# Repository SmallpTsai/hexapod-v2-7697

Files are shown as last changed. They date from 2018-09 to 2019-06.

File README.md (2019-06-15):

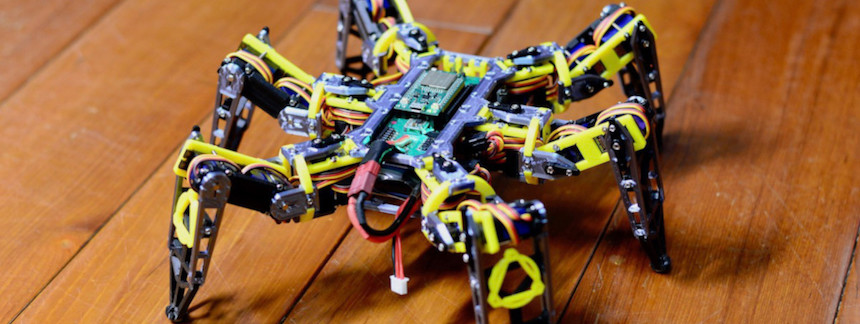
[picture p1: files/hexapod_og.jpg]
banner


# hexapod-v2-7697

> 中文版本請看 [這裡](README_tw.md)

Hexapod v2 using Linkit 7697

This is a Hexapod project.

You can use any mobile phone (iOS or Android) to control the movement of hexapod (move foreward, backward, etc...).

See demo video: https://youtu.be/NJ7DdDEcq3U & https://youtu.be/To2Y6Mhu-CE to get the idea.




> More videos can be found at https://smallptsai.github.io/hexapod-web/

## Brief introduction

* **Remote control** is done via `BLE` of `Linkit 7697`
* It has 6 legs, each leg has 3 joint. So there are total `18` **Servo motors** (TowerPro `MG92B`)
* Linkt 7697 dont have so many **PWM control**, so NXP `PCA9685` x 2 are used to control these servo motors
* **Power** comes from a `2S Lipo battery (7.4v)`. Also 7 x `mini360 DC-DC` step down voltage regulator are used. One to provide `5V` to Linkit 7697, The other six to provide `6V` to each legs (1 mini360 serve 3 servo)
* The **body** is 3D printed PLA. I use `Prusa i3 MK2S`, a really good 3D printer.
* Everything (3D STL, PCB schematic, 7697 source code) are included in the project under **GPL license**, Happy making!

## Skill requirement

If you want to make one hexapod by yourself. You should at least knows how to:

* Mechanism part
    * Use `3D printer` to print a model.
    * Able to adjust 3D model to fit your custom need.
* Electronics
    * Make a `PCB` (suggest to use professional PCB services)
    * Soldering `SMD` component (0805 and TSSOP28)
    * How to use/charge/store `LIPO batteries`
* Software
    * Use `Linkit 7697` (ie. upload and run any program)
    * Use `LRemote` to communicate 7697 and your mobile phone

## Table of Content

1. [Mechanism](mechanism/) - How to build the body
1. [Electronics](electronics/) - Circuit explanition
1. [Software](software/) - The software running on Linkit 7697

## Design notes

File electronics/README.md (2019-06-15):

# Electronics

## Connection Diagram

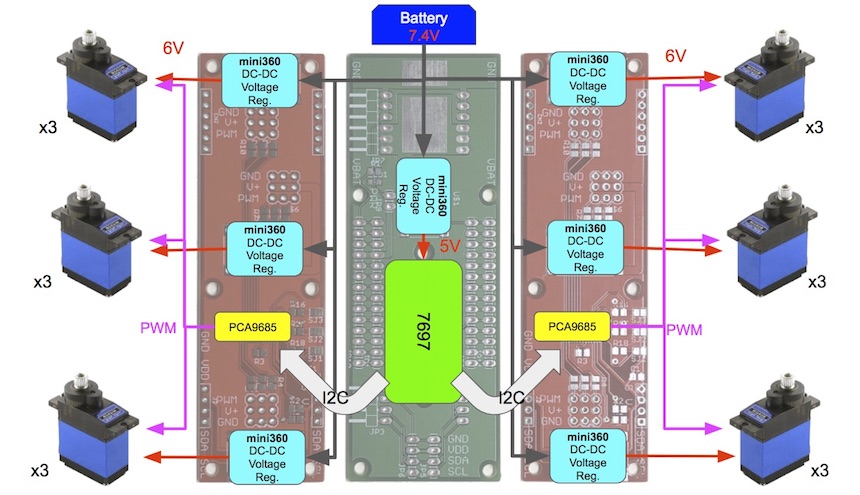
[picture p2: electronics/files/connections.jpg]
connections


## Bill of Materials (BOM)

### PCB

Name | Thumbnail | Required | Note |
-------- | --------- | -------- | ---- | 
main | main | 1 |
sub | sub | 2 | there is a difference (SJ1) between<br>the 2 PCB, refer to below

### Components

Name | Thumbnail | Required | Note |
-------- | --------- | -------- | ---- | 
[Linkit 7697](https://labs.mediatek.com/zh-tw/platform/linkit-7697) |  | 1 |
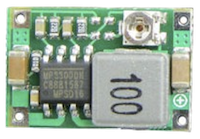
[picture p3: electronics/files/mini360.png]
[mini360 DC-DC](https://www.aliexpress.com/w/wholesale-mini360-dc-dc.html) Buck voltage regulator |  | 7 | adjust to 5V
[PCA9685](https://cdn-shop.adafruit.com/datasheets/PCA9685.pdf) (TSSOP28)|  | 2 | TSSOP28 |
Resistor: 220 ohm (0805) | | 18 | SMD |
Resistor: 10K ohm (0805) | | 12 | SMD |
Resistor: 470 ohm (0805) | | 1 | SMD |
LED: green or any color (0805) | | 1 | SMD |
Capacitor: 10 uF (0805) | | 2 | SMD |
14 pin 2.54mm female header | | 4 |
4 pin 2.54mm female header | | 2 |
6 pin 2.54mm female header | | 2 |
4 pin 2.54mm 90 degress male header | | 2 |
6 pin 2.54mm 90 degress male header | | 2 |
4 pin 2.54mm male header | | 2 |
3 pin 2.54mm male header (black) | | 6 |
3 pin 2.54mm male header (yellow) | | 6 |
3 pin 2.54mm male header (red) | | 6 |
2 pin 2.54mm male header | | 1 |
Jumper 2.54mm | | 1 |

## PCB detail

##### Software 

Please use **Eagle 7.7** software to open schematic files (main.sch/main.brd and sub.sch/sub.brd)

Eagle 7.7 can be found at http://eagle.autodesk.com/eagle/software-versions/1

    Note.
    7.7 is an old and free version of Eagle. 
    Latest Eagle is not free anymore unless you are students

##### Manufacture

There are a lot of online service that can manufacture PCB/PCBA for you (just google `PCB/PCBA`).

Seeed (https://www.seeedstudio.io/fusion_pcb.html) is one of them.

They also provide instructions of generating necessary Gerber files at http://support.seeedstudio.com/knowledgebase/articles/1176532-how-to-generate-gerber-file.

### Main

`main.brd`/`main.sch`

##### Schematic

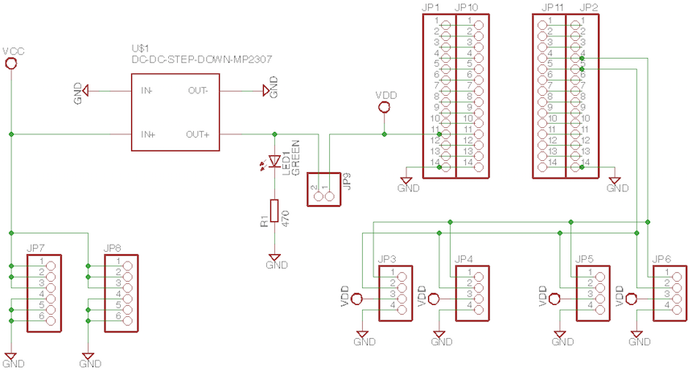
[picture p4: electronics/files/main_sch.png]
main_sch


    Note.
    `MP2307` refer to mini360 DC-DC converter

##### Layout

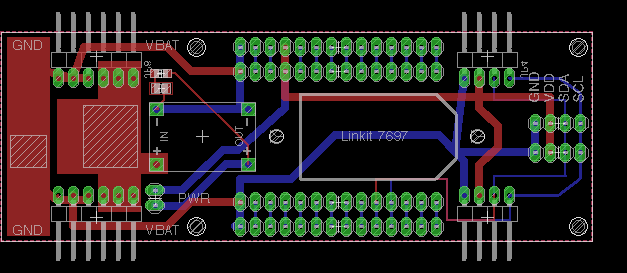
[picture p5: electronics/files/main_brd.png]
main_brd


##### PCB

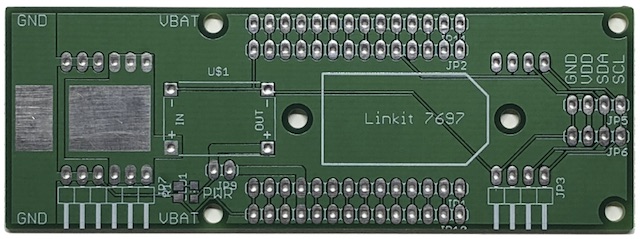
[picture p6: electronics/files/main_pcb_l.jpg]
main_pcb


### Sub (x2)

`sub.brd`/`usb.sch`

> There is 1 difference between left and right PCB. The SJ1 of right PCB is left open, but `SJ1` of left PCB should be **closed**. (This is i2c address setting of PCB9865)

##### Schematic

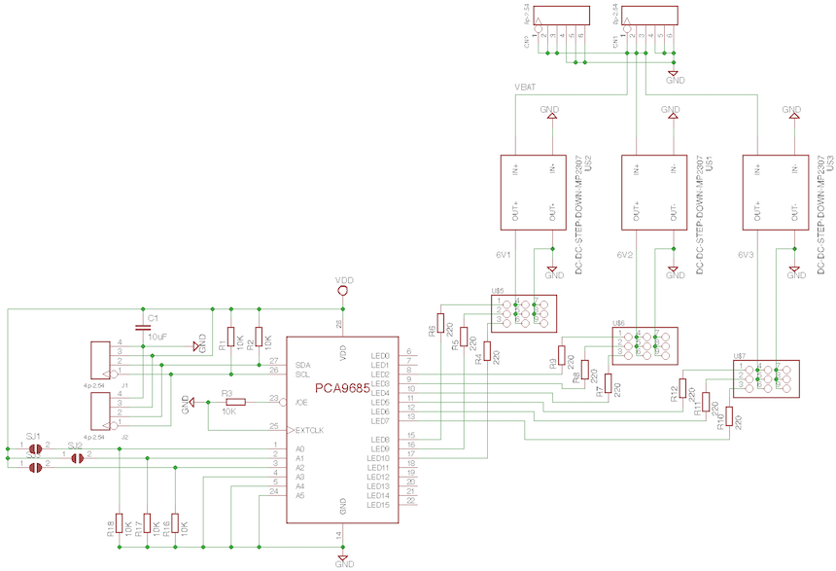
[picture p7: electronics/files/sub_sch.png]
sub_sch


    Note.
    `MP2307` refer to mini360 DC-DC converter

##### Layout

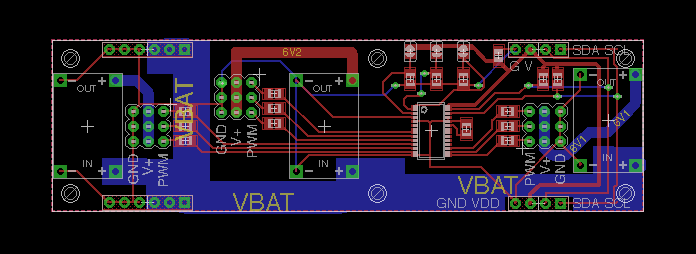
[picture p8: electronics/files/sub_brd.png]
sub_brd


##### PCB

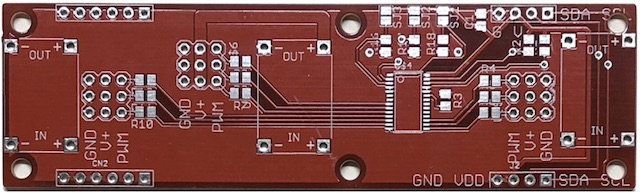
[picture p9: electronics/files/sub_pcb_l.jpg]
sub_pcb


## Servo Connection

Each leg of hexapod has 3 servos (body, thigh, foot), refer to below diagram for correct connection

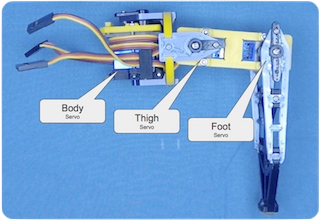
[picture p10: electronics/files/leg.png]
leg


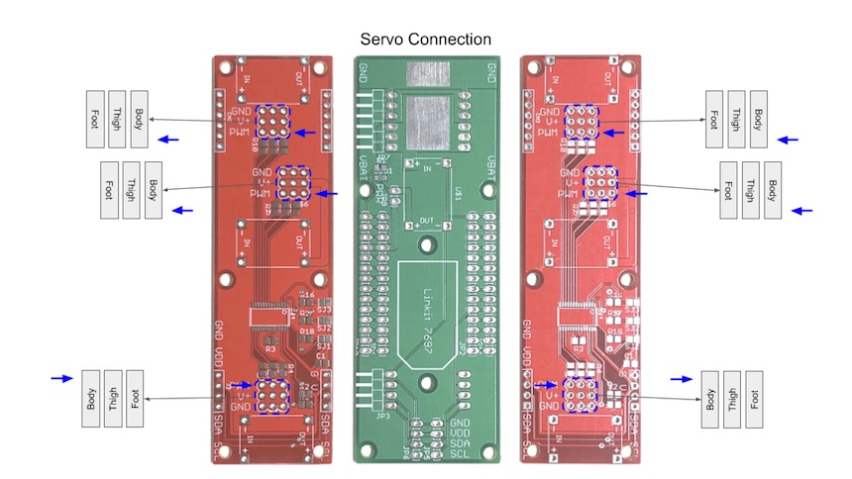
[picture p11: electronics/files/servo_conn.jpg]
servo_conn


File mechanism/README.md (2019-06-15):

# Mechanism

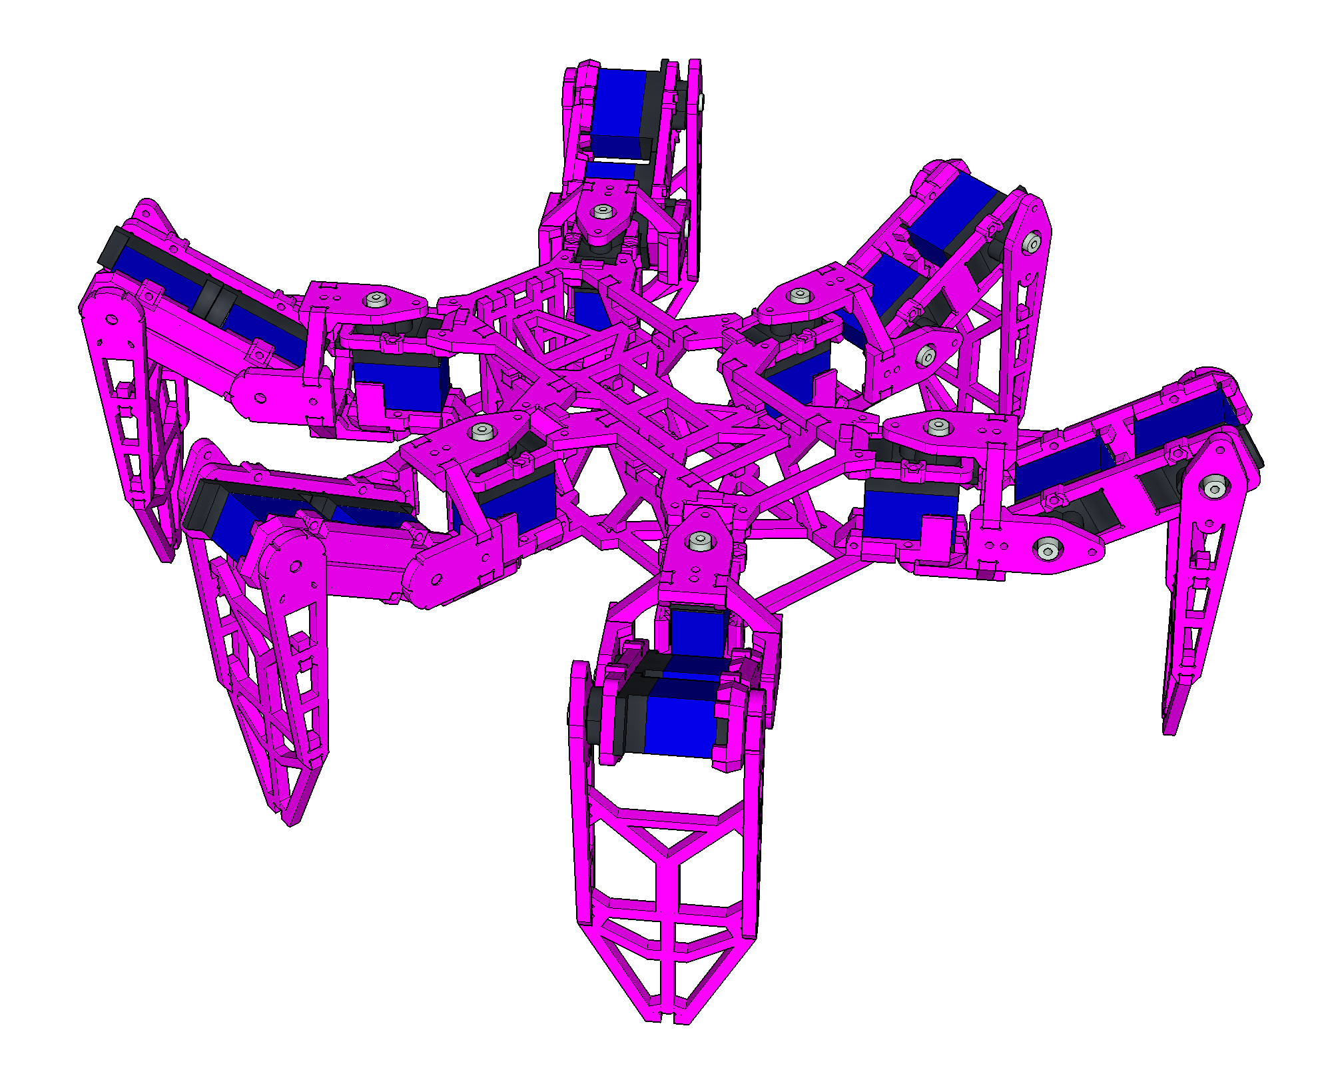
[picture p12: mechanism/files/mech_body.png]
Body


## Bill of Materials

[BOM](BOM.md)

## Leg Assemble

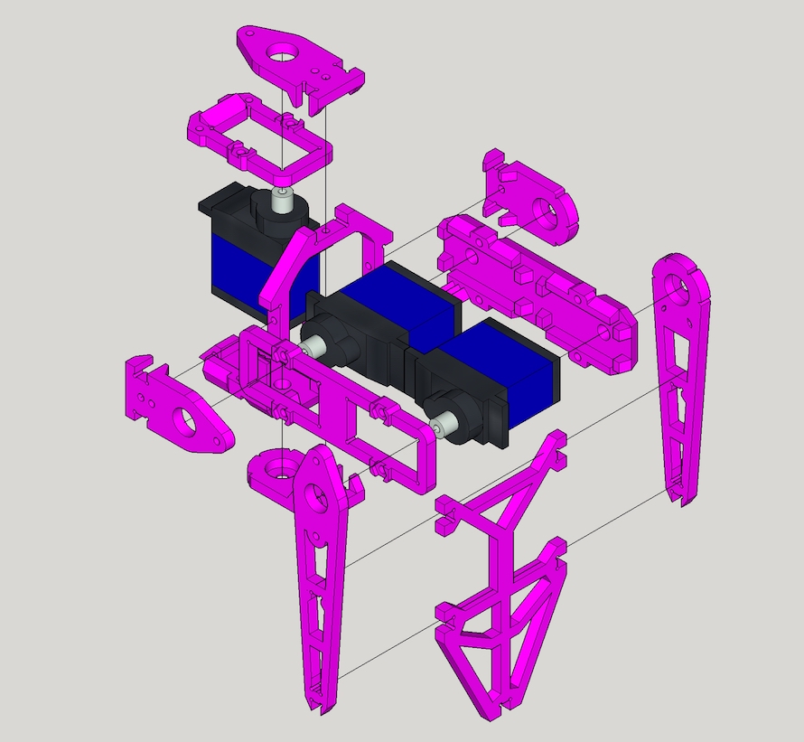
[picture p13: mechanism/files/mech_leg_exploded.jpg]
LegAssemble


Please check [Leg Assemble](LEG.md) for more detail instructions

Leg assembly instruction video https://youtu.be/oaAE5fC09KQ is also available.


> Note. Total 6 Legs are required.

## Body Assemble

TBD

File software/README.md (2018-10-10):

# Software

Software contain 2 parts, one is software of running on Linkt 7697 (an arduino C++ program), another is path generation (a python program).

* hexapod7697: an arduino program running on Linkit 7697
* pathTool: a python program that generate 3D points header, included by `hexapod7697`

## hexapod7697

Files/Folder | Description |
------------ | ----------- |
src/normal_mode | provide normal calibration (forward/backward/turn left/turn right/rotate/etc...) |
src/setting_mode | provide calirbration functions, to make sure servo is correctly aligned. |
src/linkit_control/ | UI control helper |
src/hexapod | hexapod class |
src/hexapod/hal | Hardware Abatraction Layer to running on Linkit 7697 |

> Note hexapod7697 use c++11 and STL, you may encounter problem if want to port it on pure Arduino platform.

#### Normal Mode UI

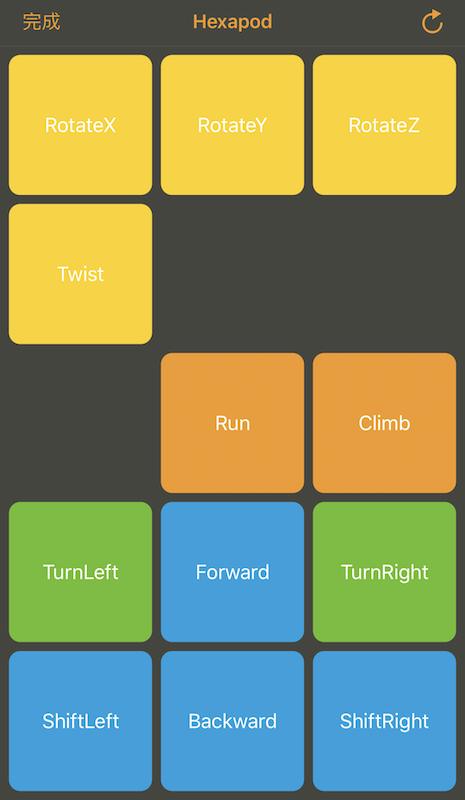
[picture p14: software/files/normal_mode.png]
normal


#### Setting (Calibration) Mode UI

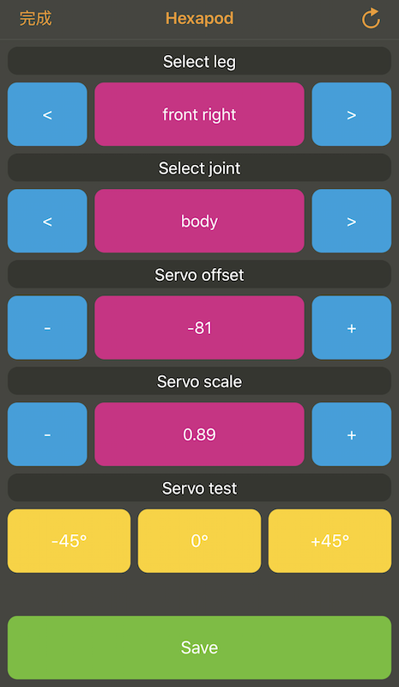
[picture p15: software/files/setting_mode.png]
setting


During Linkit 7697 boot up, quick press the user button. 

LRemote App will display above UI.

It is used to adjust the settings of each servo, make sure they align to center.

> Note. Dont press user button when power on, but just after power on.

## pathTool

* Python compatibility:
    * 3.x: ok.
    * 2.x: not verified. 
* Required package
    * numpy: `pip3 install numpy`

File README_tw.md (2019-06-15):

banner

# hexapod-v2-7697

Hexapod v2 using Linkit 7697

這是個 Hexapod (六足昆蟲) 專案

可以用任何手機 (iOS 或 Android) 來控制它的動作 (包括前進，後退，扭動等等...)

可參考以下的 Youtube 影片 https://youtu.be/NJ7DdDEcq3U & https://youtu.be/To2Y6Mhu-CE




> 在 https://smallptsai.github.io/hexapod-v2-7697/ 可以看到更多影片

## 簡介

* 利用 `Linkit 7697` 的 `BLE` 藍牙功能來作到 **遙控**
* 它有六隻腳，每隻腳各有三個關節，總共使用了 `18` 個 **伺服馬達** (TowerPro `MG92B`)
* Linkit 7696 沒有這麼多個 PWM 可用，所以使用了二顆 NXP 的 `PCA9685` 來控制這麼多個伺服馬達
* 動力使用 7.4v 的鋰電池 `2S Lipo battery (7.4v)`, 另外也用了 7 個 `mini360 DC-DC` 穩壓電路，其中 1 個供電給 Linkit 7697, 其它 6 個各負責一隻腳 (三個伺服馬達) 的電力
* 機身則使用 3D 列印 (PLA材質)
* 所有東西  (模型STL檔案, PCB電路圖, 7697代碼) 都以 GPL license 開源, Happy making!

## 技能需求

如果你也想要實現這個專案，會需要以下的技能:

* 機構部分
    * 會使用 `3D 列印`
    * 能夠微調 3D 模型以符合自己的需求 (例如, 使用不同的伺服馬達)
* 電路部分
    * 洗 `PCB` 電路板 (建議找專業 PCB 服務)
    * 焊接 `SMD` 元件 (0805 和 TSSOP28 封裝)
    * 知道如何使用鋰 (`Lipo`) 電池 (充電和保存)
* 軟體部分
    * 使用 `Linkit 7697` (ie. 編譯和上傳程式)
    * 使用 `LRemote` 來連接 7697 和手機

## Table of Content

1. [機構](mechanism/) - 如何組裝3D件 (English only)
1. [電路](electronics/) - 電路說明 (English only)
1. [軟體](software/) - 7697上的軟體 (English only)

## FAQ

1. 如何校正 / 為什麼腳的位置不正

    Calibration 在軟體內有內建, Reboot 後時按一下 7697 上的 USR key, 再用手機連會進到另一個 UI, 可以針對每個 Servo 去調中心點 (offset) 和 比例 (scale), 3d 件上都有個溝槽可以對 0度, 45度和 -45度, 對好後再按 Save 存檔

1. Servo 如何連接, 順序是什麼

    順序都是由內到外, body -> thigh -> foot，不過 layout 時會了走線好看, 有一隻腳的方向是反的，可以在 calibration 時切到不同位置按 45~0~-45度動看看來調整
    請參照 [electronics/#servo-connection](electronics/#servo-connection)

1. 在調整/校正時，左右 Servo 連動，正常嗎?

    不正常, 左右兩張板子有一個地方 (i2c address) 不同，左邊的PCB板的 SJ1 要焊起來
    請參照 [electronics/#sub-x2](electronics/#sub-x2)

1. 請問校正的標準姿勢為何? 例如人形立正或大字型

    所有的關節都在 0 度的位置, 是個 ㄇ 型
    校正要先回到 offset/scale 0 的情況, 再重鎖 servo 擺臂盡量到置中位置後，再用軟體微調~

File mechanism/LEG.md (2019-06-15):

# Leg Assemble Instruction

Leg assembly instruction video https://youtu.be/oaAE5fC09KQ is also available.


## Preparation

For one leg, you will need 3 MG92B servo and below printed parts

Filename | Thumbnail | Required |
-------- | --------- | -------- |
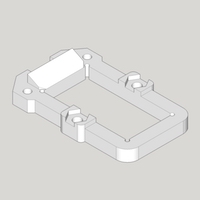
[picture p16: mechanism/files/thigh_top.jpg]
thigh_top
thigh_top |  | 1 |
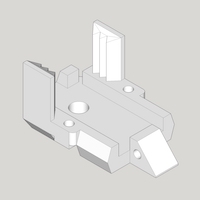
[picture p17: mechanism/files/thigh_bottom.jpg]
thigh_bottom
thigh_bottom |  | 1 |
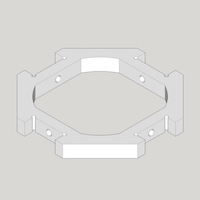
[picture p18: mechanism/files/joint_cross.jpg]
joint_cross
joint_cross |  | 1 |
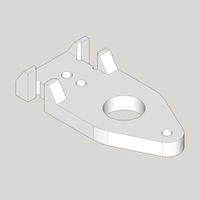
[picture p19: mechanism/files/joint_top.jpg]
joint_top
joint_top |  | 2 |
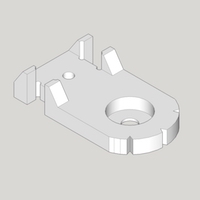
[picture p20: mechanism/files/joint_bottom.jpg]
joint_bottom
joint_bottom |  | 2 |
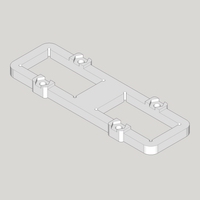
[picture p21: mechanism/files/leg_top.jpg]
leg_top
leg_top |  | 1 |
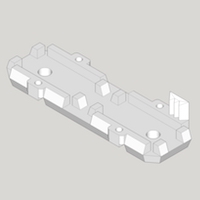
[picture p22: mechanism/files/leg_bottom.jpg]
leg_bottom
let_bottom |  | 1 |
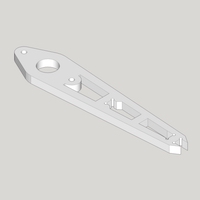
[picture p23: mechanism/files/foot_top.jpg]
foot_top
foot_top |  | 1 |
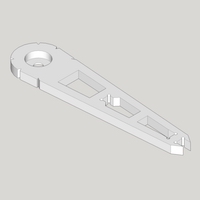
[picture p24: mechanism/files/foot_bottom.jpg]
foot_bottom
foot_bottom |  | 1 |
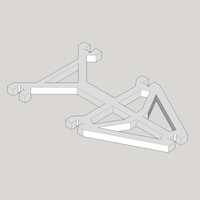
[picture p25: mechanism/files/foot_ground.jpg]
foot_ground
foot_ground |  | 1 |
foot_tip | foot_tip | 1 |

## Step 1

LegAssemble1

Combine `thigh_top`, `MG92B` and `thigh_bottom`, use M2x30mm screw and nut to secure them together.

## Step 2

LegAssemble2

Grab one `joint_cross`, `joint_top` and `joint_bottom` and combine them

## Step 3

LegAssemble3

First put 2 x `MG92B`, `leg_top` and `leg_bottom` together with M2x30mm screw and nut.
Then attach `joint_top` and `joint_bottom` altogether

## Step 4

LegAssemble4

Grab `foot_top`, `foot_bottom` and `foot_ground` (and `foot_top`) and assemble them.

## Finish!

LegAssemble5

Great, you got 1 leg done, 5 more to go :)

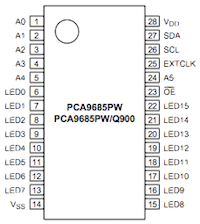
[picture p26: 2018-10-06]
electronics/files/pca9865.png

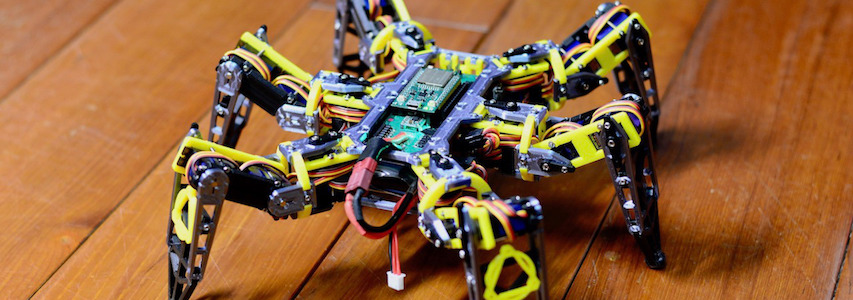
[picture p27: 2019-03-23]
docs/images/jumbotron-bg.jpg

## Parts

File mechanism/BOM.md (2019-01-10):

# Bill of Materials

## Servo - MG92B

Servo is the key component. I use TowerPro [MG92B](http://www.towerpro.com.tw/product/mg92b/). It has metal gear (important!).
An hexapod requires 18 of them.

>    The dimension of 3d printed part is highly depended on servo's dimension.<br>
>    Modification is required if you want to use other alternative servo. 

>    TowerPro MG92B can be found on Ebay seller [servohorns959](https://www.ebay.com/usr/servohorns959), which is listed on TowerPro official website ([Link] (http://www.towerpro.com.tw/about-us-2/)). <br>I also got mime servo from him.

## 3D-Printed Parts

### Body x 1

Filename | Thumbnail | Required |
-------- | --------- | -------- |
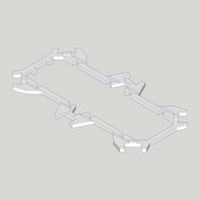
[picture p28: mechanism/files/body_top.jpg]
body_top
body_top |  | 1 |
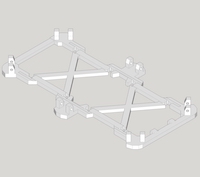
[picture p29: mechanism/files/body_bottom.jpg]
body_bottom
body_bottom |  | 1 |
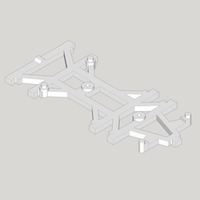
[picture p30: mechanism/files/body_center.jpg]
body_center
body_center |  | 1 |
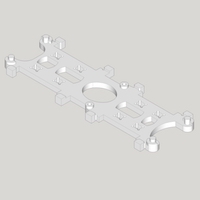
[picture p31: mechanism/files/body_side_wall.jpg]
body_side_wall
body_side_wall |  | 2 |
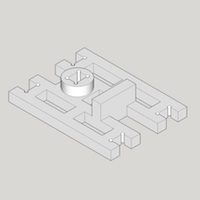
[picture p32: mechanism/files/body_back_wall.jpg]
body_back_wall
body_back_wall |  | 1 |

### Leg x 6

Filename | Thumbnail | Required |
-------- | --------- | -------- |
thigh_top | thigh_top | 1 (x6) |
thigh_bottom | thigh_bottom | 1 (x6) |
joint_cross | joint_cross | 1 (x6) |
joint_top | joint_top | 2 (x6) |
joint_bottom | joint_bottom | 2 (x6) |
leg_top | leg_top | 1 (x6) |
let_bottom | leg_bottom | 1 (x6) |
foot_top | foot_top | 1 (x6) |
foot_bottom | foot_bottom | 1 (x6) |
foot_ground | foot_ground | 1 (x6) |
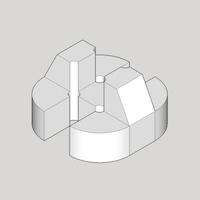
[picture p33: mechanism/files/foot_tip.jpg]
foot_tip
foot_tip |  | 1 (x6) |

## Others

Name | Spec | Thumbnail | Required | Note
---- | ---- | --------- | -------- | ----
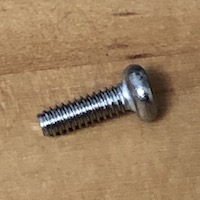
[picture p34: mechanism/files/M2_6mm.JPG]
Screw | M2 6mm |  | 54 | Servo Arm: 1 x 18<br>Joint: 4 x 6<br>Thigh: 2 x 6
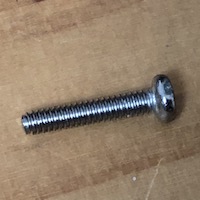
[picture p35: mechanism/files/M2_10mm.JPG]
10mm
Screw | M2 10mm |  | 24 | Thigh: 1 x 6<br>Pin lock: 1 x 18
Screw | M2 30mm | 30mm | 36 | Servo: 2 x 18
Nuts | M2 | 6mm | 36 | Servo: 2 x 18
Pin (304) | M4 6mm | pin | 18 | Servo: 1 x 18

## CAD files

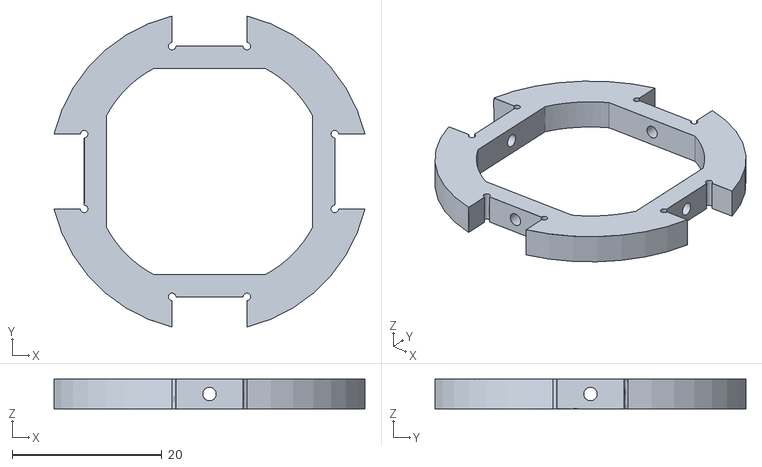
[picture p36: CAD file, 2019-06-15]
mechanism/joint_cross.stl
41.6 x 41.6 x 4.00

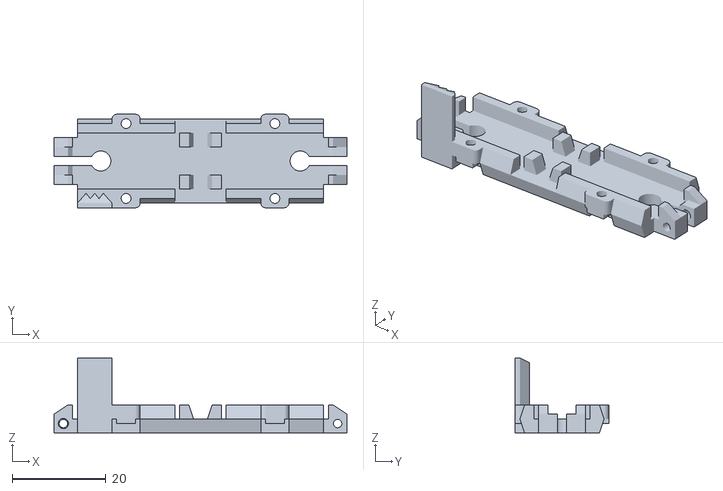
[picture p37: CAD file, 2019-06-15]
mechanism/leg_bottom.stl
62.6 x 20.0 x 16.0

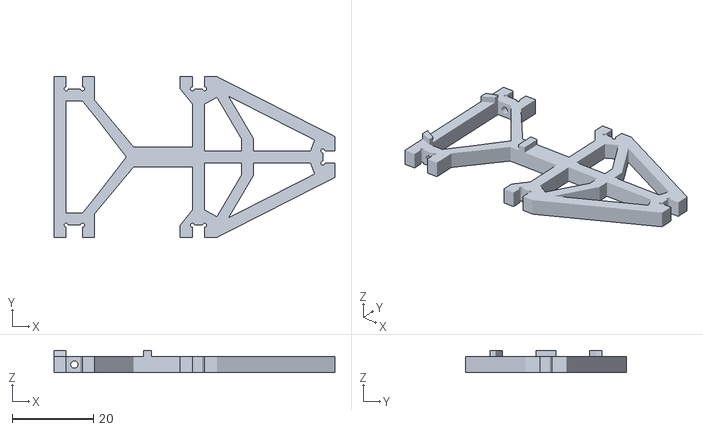
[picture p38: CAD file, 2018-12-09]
mechanism/foot_ground.stl
69.0 x 39.5 x 5.50

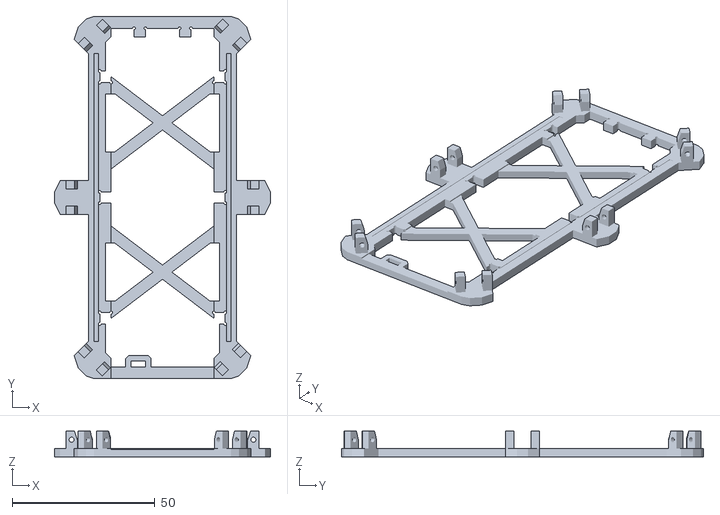
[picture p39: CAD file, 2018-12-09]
mechanism/body_bottom.stl
75.7 x 127.0 x 9.00

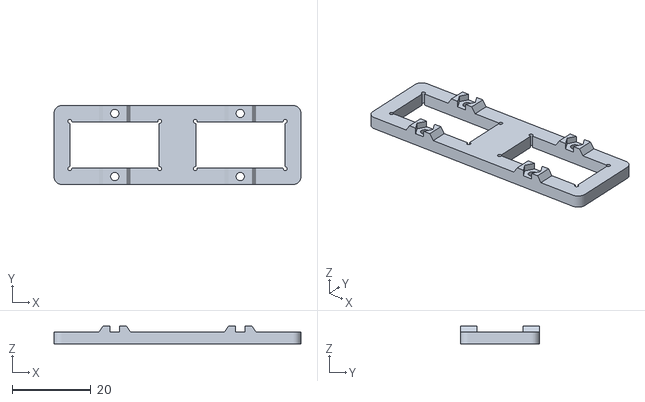
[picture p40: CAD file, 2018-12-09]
mechanism/leg_top.stl
62.6 x 20.0 x 4.50

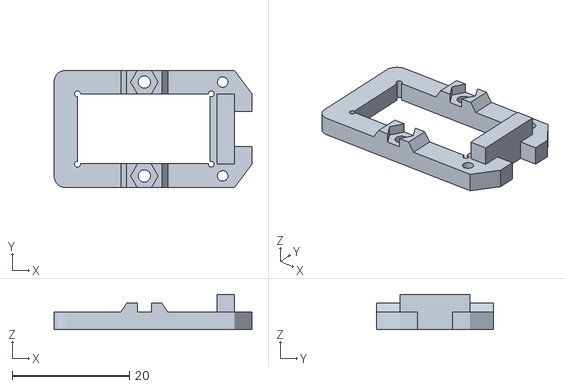
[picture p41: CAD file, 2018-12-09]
mechanism/thigh_top.stl
33.8 x 20.0 x 6.00

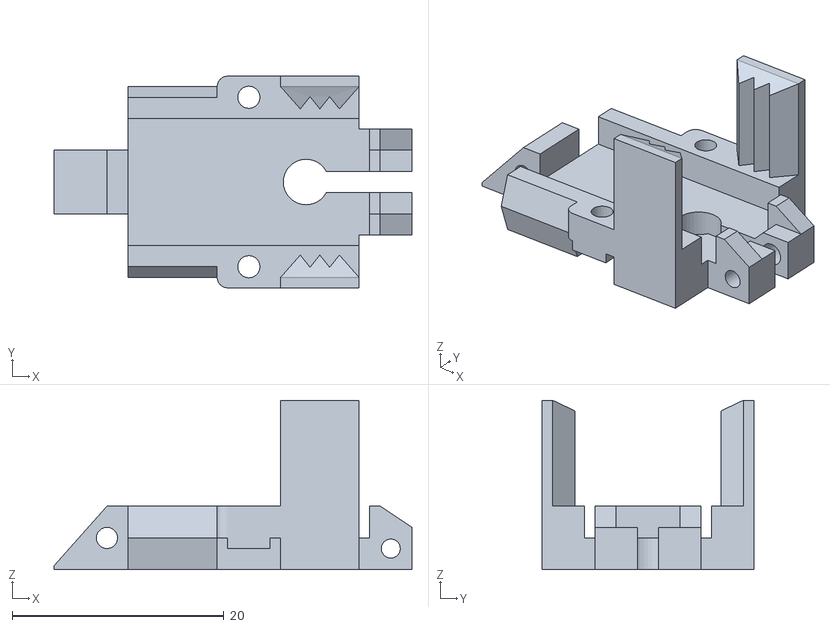
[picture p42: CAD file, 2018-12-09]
mechanism/thigh_bottom.stl
33.8 x 20.0 x 16.0

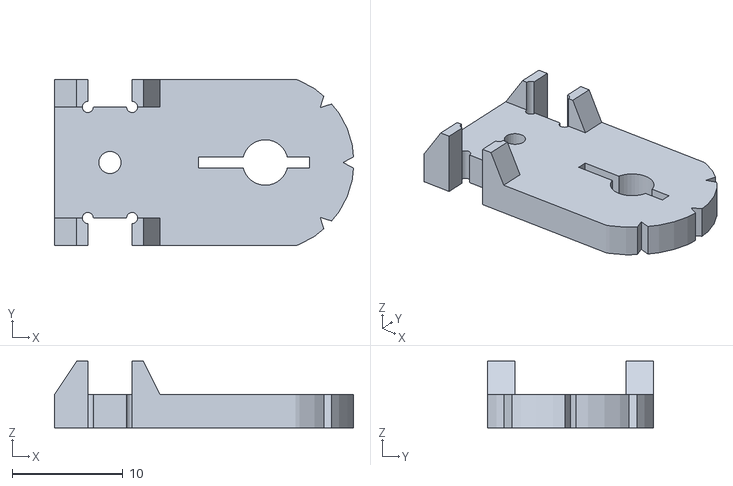
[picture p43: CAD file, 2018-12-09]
mechanism/joint_bottom.stl
27.0 x 15.0 x 6.00

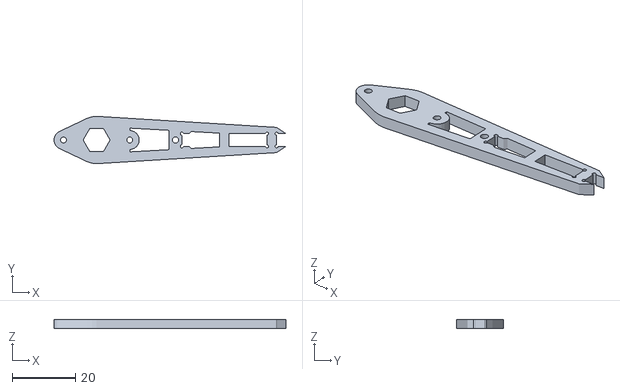
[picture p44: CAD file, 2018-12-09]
mechanism/foot_top.stl
73.5 x 15.0 x 3.00

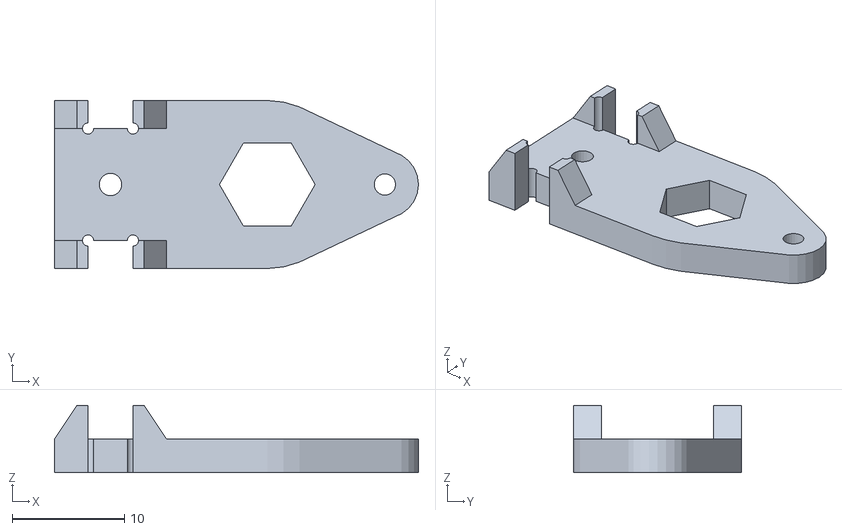
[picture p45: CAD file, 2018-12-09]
mechanism/joint_top.stl
32.5 x 15.0 x 6.00

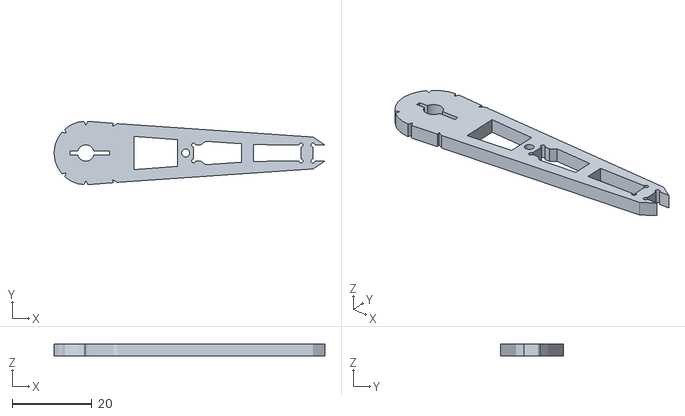
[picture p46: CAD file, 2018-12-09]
mechanism/foot_bottom.stl
68.1 x 15.9 x 3.00

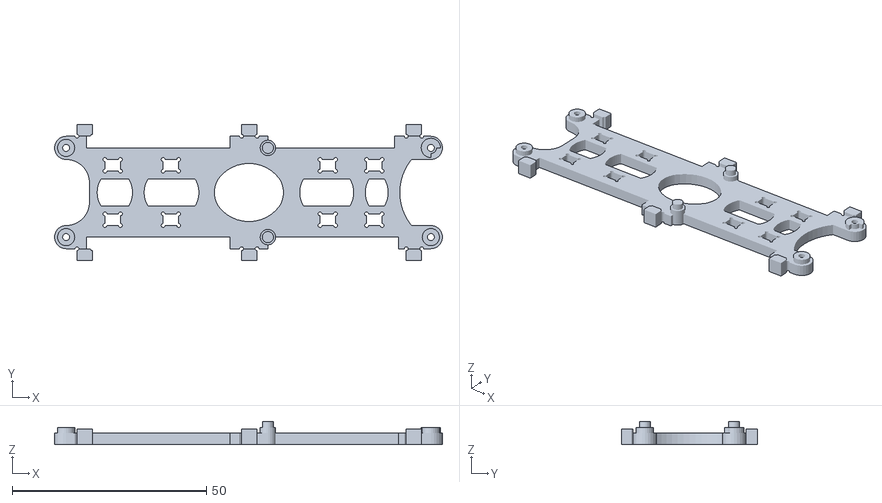
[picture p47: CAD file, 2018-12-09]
mechanism/body_side_wall.stl
100.0 x 35.0 x 6.00

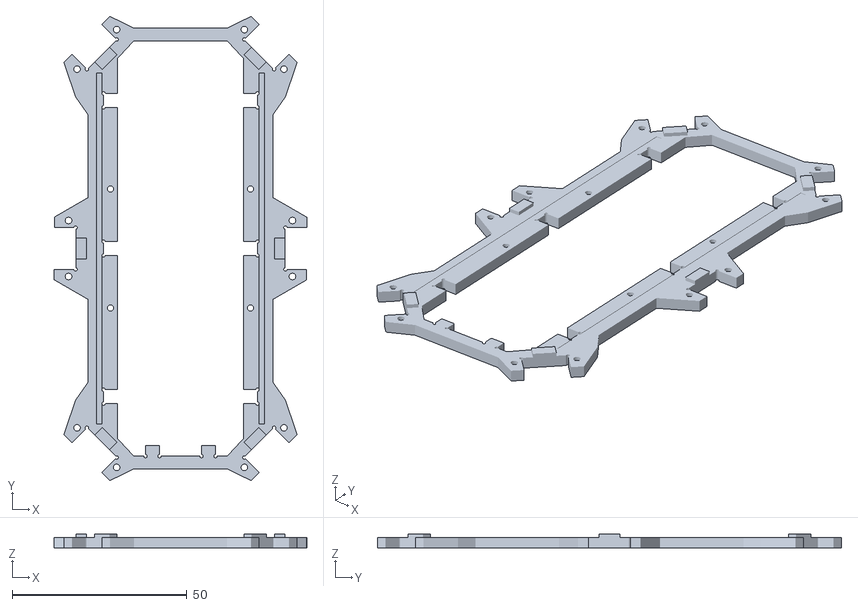
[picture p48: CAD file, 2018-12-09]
mechanism/body_top.stl
72.3 x 132.7 x 4.00

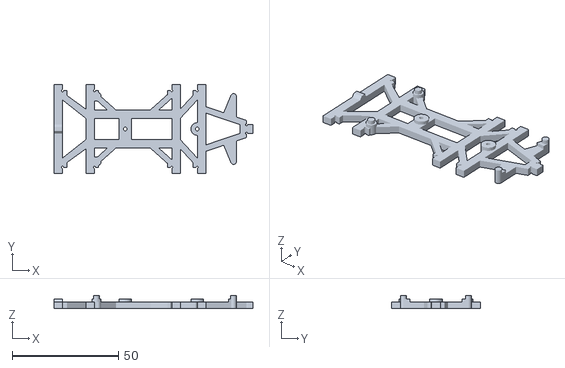
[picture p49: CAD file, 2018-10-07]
mechanism/body_center.stl
93.6 x 42.0 x 6.00

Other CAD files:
mechanism/foot_tip.stl
mechanism/battery_lock.stl
mechanism/tools_mount.stl
mechanism/body_back_wall.stl

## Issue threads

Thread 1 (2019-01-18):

servos direction

chris666uk1, 2019-01-18:
hi i am using MG92b servos but they seem to be the wrong direction i calibrated them straigt but when pluged in they travel upwards

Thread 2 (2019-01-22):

Red CircBoards

mistermhaas, 2019-01-22:
In the connection diagram is a red Circboard. Which one is this in the BOM? And can i have a picture of the Conection boards with the wires

vertigo475, 2020-08-14:
hi you can read the post I have made on the issues "my first electronic project" i've put a picture of the main and sub boards. The only connexion between main and sub are 2x4 and 2x6 pin all the rest is include in the subboards.

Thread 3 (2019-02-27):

leg_bottom broken

niyawe, 2019-02-27:
Hi,

it seems the leg_bottom.stl is broken:

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

khenderick, 2019-05-15:
I had also difficulties printing that one. I managed to fix it on https://tools3d.azurewebsites.net/

You can download it in #5

MRCamiloLagos, 2020-12-04:
i need help i need the screws where i can get? can you give a link i think the size is 1M

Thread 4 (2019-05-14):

Corrupt/unprintable joint_cross.stl

khenderick, 2019-05-14:
The model `join_cross.stl` seems to be broken. A first indication is that pictures of your hexapod and the images in the repo show the corners flat, while my slicer and certain stl viewers display it with rounded corners.

It seems fusion 360 can't automatically repair it, and I couldn't figure out the exact measurements to redraw it.

Any possibility you can re-export it?

jmfinn9, 2019-05-15:
Does this look better? I ran it through makeprintable.com
[fixed_stl_joint_cross.zip](https://github.com/SmallpTsai/hexapod-v2-7697/files/3180500/fixed_stl_joint_cross.zip)

khenderick, 2019-05-15:
Looks and slices perfect. Thanks a lot :smile: . I tried a bunch of online repair services myself, but good to know this one managed to fix the issues.

Closed 2019-06-15.

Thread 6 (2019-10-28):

use servo sg90 instead MG92B

pindarogb, 2019-10-28:
thanks

ArvinRoad, 2020-11-29:
我也有这样的疑问，sg90的伺服可以代替Mg92b吗？

kooliha, 2021-09-02:
+1 The same question

Can MG90D use instead of MG92B? Size is a bit different and torque for sure
https://www.towerpro.com.tw/product/mg92b/
https://www.towerpro.com.tw/product/mg90d-2/

ValeraDanger, 2022-01-04:
I am using mg90s (analog of sg90s with metal gears). They have same size like mg92b, but hight is smaller. I already made one leg and all right. But you have to use little bit longer pins (about 8mm). The only one problem I see - connection legs to the main part. Body is thicker then legs. But I think, this problem will be solved.

Omarinh, 2022-01-17:
>

so do you use sg90s instead of mg92b and the hexapod still move
im afraid it's too heavy for that servo

ValeraDanger, 2022-01-17:
>

No, I'm using mg90s. This is sg90s, but only with metal gears. I have already made only mechanical part. It is rather lightweight (540g with all my servos without battery and electronics). Robot standing without any powering, so there willn't a problem for servos, I think.

Omarinh, 2022-01-17:
540 g without battery and eletronics i think they are the most of the weight but this is a bit reassuringthanks

Omarinh, 2022-01-17:
> 540 g without battery and eletronics i think they are the most of the weight but this is a bit reassuring, thanks for info

ValeraDanger, 2022-01-18:
> > 540 g without battery and eletronics i think they are the most of the weight but this is a bit reassuring, thanks for info

I will use 4*18650. It is about 200g. Esp32 and pwm controllers have no weight in this situation. Robot is weighing less kg. It is  normal for 18 mg90s, IMHO)
But I recommend you use metal servos anyway

Omarinh, 2022-01-18:
Okay thanks, esp32 has more pwm do you use  two pca9685 anyway?

ValeraDanger, 2022-01-18:
> Okay thanks, esp32 has more pwm do you use two pca9685 anyway?

It has 16 pwms, I need 18 :)
Yeap, I'm using 2 pca9685. I think, the code will be quite unreadable, if some servos Wil be on esp32, and some on pca9685

Omarinh, 2022-01-18:
Okay thanks i forgot to see the pinout of the esp32 :)

UlrichKlotzsche, 2022-11-05:
> I am using mg90s (analog of sg90s with metal gears). They have same size like mg92b, but hight is smaller. I already made one leg and all right. But you have to use little bit longer pins (about 8mm). The only one problem I see - connection legs to the main part. Body is thicker then legs. But I think, this problem will be solved.

I altered the thigh_bottom so that the thigh fits to the body, when you use MG90s servos. Here you go: https://github.com/UlrichKlotzsche/Hexapod-TowerPro_MG90s/blob/main/thigh_bottom_MG90s.stl

As I am new to 3D Printing and CAD, this is not perfect but it works for me.

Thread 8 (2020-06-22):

> There is 1 difference between left and right PCB. The SJ1 of right PCB is left open, but `SJ1` of left PCB should be **closed**. (This is i2c address setting of PCB9865)

dirk-asam, 2020-06-22:
Could you explain me what a SJ1 is? Is it an electronic part?

Thank you

jmfinn9, 2020-06-23:
I think it's a solder or surface jumper on the board evidently that's how the main board tells these two apart via i2c

dirk-asam, 2020-08-06:
Helped me- Thanx

Closed 2020-08-06.

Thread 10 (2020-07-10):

My first electronic project.

vertigo475, 2020-07-10:
I would like to thank you for all the detail given. It was my first electronic project and it' a success...

I've ordered the pcb with your files and a success again.

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

Thanks for sharing, very good quality of files.

Olivier

carlo5, 2020-07-26:
Hi, I wanted to ask you about a doubt in the assembly, you ordered the PCB already with the parts installed or did you install them. Because I have looked at the entire project, but I cannot find something that indicates the correct order of assembly according to its components . I just found the list of components. Or if somewhere you found BOM file (Bill of Materials) to be assembled by the PCB manufacturer.
I already appreciate the response and sorry for the inconvenience.
A big greeting from Argentina

carlo5, 2020-07-26:
Hi, that's good! It looks very well assembled, I congratulate you! I wanted to ask you about a doubt in the assembly, you ordered the PCB already with the parts installed or I install them because I have looked at the entire project, but I cannot find something that indicates the correct order assembly according to its components. Or if somewhere you found BOM file (Bill of Materials) to be assembled by the PCB manufacturer.
I already appreciate the response and sorry for the inconvenience.
A big greeting from Argentina

carlo5, 2020-07-26:
Hi, that's good! looks very well armed, congratulations! I'm trying to build one, and I wanted to ask you about a question that I have in the assembly, you ordered the PCB already with the parts installed or you installed them because I have looked at the entire project, but I can't find something that indicates the correct order assembly according to its components. Or if somewhere you found BOM file (Bill of Materials) to be assembled by the PCB manufacturer.
I already appreciate the response and sorry for the inconvenience.
A big greeting from Argentina

vertigo475, 2020-07-26:
Hi,
you Will find the BOM under the link below,
https://github.com/SmallpTsai/hexapod-v2-7697/blob/master/electronics/README.md

I had for reference for what to solder where on the files BRM (indications to order pcb boards). I start personnally oy the most little pieces (2 smallest with 2x14 pins) and after the SMD components at least the mini dc, and the 2.54 pins. It Wars my first project so i take a microscope to solder it proprely, with a really small iron and a lot of patience 😀

I don't Know if the manufacturer can assemble it.  I order them without components by first pcb in Hong Kong with good quality and fast delivery and good price. I order 10 pieces of subboard and 5 pieces of main board in case of bullshit solder.

At your disposal for questions, regards from switzerland

Olivier Corbaz

Le 26 juil. 2020 à 04:34, carlo5 <notifications@github.com<mailto:notifications@github.com>> a écrit :

Hi, I wanted to ask you about a doubt in the assembly, you ordered the PCB already with the parts installed or did you install them. Because I have looked at the entire project, but I cannot find something that indicates the correct order of assembly according to its components . I just found the list of components. Or if somewhere you found BOM file (Bill of Materials) to be assembled by the PCB manufacturer.
I already appreciate the response and sorry for the inconvenience.
A big greeting from Argentina

—
You are receiving this because you authored the thread.
Reply to this email directly, view it on GitHub<https://github.com/SmallpTsai/hexapod-v2-7697/issues/10#issuecomment-663927836>, or unsubscribe<https://github.com/notifications/unsubscribe-auth/AQHWA5S727CTQEYTN6GDKDDR5OI3VANCNFSM4OWUUTCA>.

wudikukuqi, 2020-08-16:
Why do I make it according to the routine, but can't drive mg92b to run after starting，Software upload, signal waveform is no problem，Have you ever encountered such a situation

wudikukuqi, 2020-08-19:
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

Why do I make it according to the routine, but can't drive mg92b to run after starting，Software upload, signal waveform is no problem，Have you ever encountered such a situation

vertigo475, 2020-08-19:
Hi, did you put the jumper in the 2 pins of the main board, just near the development card ?
Did you have the connexion with the appli for phone ?

wudikukuqi, 2020-08-20:
> Hi, did you put the jumper in the 2 pins of the main board, just near the development card ?
>
> Did you have the connexion with the appli for phone ?

Thank you for your reply. I replaced the jumper on the main board with a switch. Applications can be properly connected to the development board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

vertigo475, 2020-08-20:
Excellent ! Enjoy ! 👍🏻

wudikukuqi, 2020-08-20:
> Excellent ! Enjoy ! 👍🏻

I'm sorry I didn't make it clear yesterday, Although the app can connect to the phone,But it still can't drive the MG92B.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

vertigo475, 2020-08-21:
I remember one of the 2 sub boards have a difference by join 2 points with soldering somewhere like in this pictures, did you make it ?
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

vertigo475, 2020-08-21:
I don't remember exactly where, it could be a solution. Sorry but I'm limited in electronics capabilities 😉

as321654987, 2020-09-16:
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

were you able to find the problem? I think I am having the same problem as you did. I was able to run the servos on the initial test run but after calibrations, the servos are not responsive and more.

wudikukuqi, 2020-09-20:
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

I'm very sorry that I can't help you for the time being, because I haven't found out what's wrong.

Handschrauber, 2020-10-19:
I have the same problem.
During the first test run, the Hexapod stopped after a short time and did not move until it was restarted, and it has not moved at all since the calibration.
The Arduino IDE gives me some errors when compiling, which are probably related to it. Since I am not familiar with programming, I do not know where the problem is and how I can fix it.

Can anybody help me further?
[Arduino Error.txt](https://github.com/SmallpTsai/hexapod-v2-7697/files/5403360/Arduino.Error.txt)

vertigo475, 2020-10-19:
Hi,
Sorry for your experience.
I don't had this problem. It was my first arduino project then I spend a lot of time to find the right parameter in arduino ide. But when I found it and the libraries at the right place. It goes straight right without errors in ide and without touching the code. If it could help you I can send screenshots of the parameters ? I don't know if it can help !

Anybody can help Handschrauber for this matter ?

🤞🏻🤞🏻🤞🏻

Screwmaster37, 2020-10-20:
Thank you for your prompt reply,

I would like to try it with the right parameters.
With which versions of Arduino and LinkIT was the project developed?

I've noticed that "Examples for Linkit 7697" / .LRemote / RemoteControl get similar error messages when compiling.

Could it be that the .LRemote library has changed?

Thanks for the support

vertigo475, 2020-10-20:
Hi,
It's reason why I bought the "Linkit 7697" it's easier to setup if exactly the same than original.
With the LRemote and Linkit 7697, just push the code in linkit and charge LRemote and all allright.

With different programmation card I' haven't any experience (juste one little tool with arduino nano). Sorry.

Good Luck !
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
kinghlovo, 2021-02-13:
Hi,do you know what software the Android phone uses to control this? I am a little puzzled seeing so many python programs

vertigo475, 2021-02-13:
@kinghlovo pls find the image below with details. I take the LinkIt remote control.
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

kinghlovo, 2021-02-13:
@vertigo475 Thank you very much, hope I can make it soon

dirk-asam, 2021-02-19:
Hello Vertigo,

do you have another 3 of these boards (1 Main board, 2 sub boards) you had used? The boards I have bought are wrong (some connections are wrong or not there).
P.S. it‘s also my first electronic board
Best regards Dirk

vertigo475, 2021-02-19:
@dirk-asam,

hi, yes I have 3 main boards and 6 sub boards left, avaiable if needed.

We can talk about that per mail directely  --> vertigo475@hotmail.com..

Best regards, Olivier

carlosimparato, 2021-06-05:
Buenas tardes. Después de leer todos los comentarios aún no he podido lograr subir el programa a la linkit.

vertigo475, 2021-06-06:
Hi,
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

carlosimparato, 2021-06-06:
es primera vez que trabajo con linkit y no se como pasarlos programas a la placa.
no se conecta a mi pc. linkit remote no reconoce la placa. hay que hacer algo previo?

vertigo475, 2021-06-06:
Olà,
It was my first time too with LinkIt, I used ide arduino to link with the pc and put the downloaded code into LinkIt. Once the code in, the connection with the app come automatically. To import the libraries in LinkIt. I followed a tutorial find in internet / YouTube. Possible some can help more Carlo in this discussion ? Hope so...🤞🏻

carlosimparato, 2021-06-06:
gracias vertigo475

jyothisvikram, 2021-06-09:
Thank you vertigo475 for all your support above. I am not able to find a place where I can buy Linkit 7697. Any idea where I can buy it?

wudikukuqi, 2021-06-10:
> Thank you vertigo475 for all your support above. I am not able to find a place where I can buy Linkit 7697. Any idea where I can buy it?

ebuy

wudikukuqi, 2021-06-10:
> > Thank you vertigo475 for all your support above. I am not able to find a place where I can buy Linkit 7697. Any idea where I can buy it?
>
>

You can buy it on ebuy, but it's super expensive. I bought three without a large-scale price increase.

vertigo475, 2021-06-10:
Here in switzerland we cay buy it for approx 25 us without sending costs www.galaxus.ch. Comes very quickly...

jyothisvikram, 2021-06-10:
Thank you for the update... I can’t find any here who got that! Have any of you used any other Arduino chip for this project?

carlosimparato, 2021-06-12:
no se puede realizar con otra placa porque todo el circuito de las PCB estan realizadas para el 7697,  yop tengo el linkit 7697 y el 7688 pero el 7697 no logro hacer que mi pc lo reconozca. no se porque.

carlosimparato, 2021-06-12:
necesito saber si mi placa de linkit 7967 esta buena. ustedes cuando conectan la placa a la computadora, es reconocida automáticamente? Gracias

vertigo475, 2021-06-12:
It depends with which program do you work with. With ide arduino you have to setup a bit. I don't know how it is withe the others programs. It a long time ago but I found a video in YouTube explaining how to link LinkIt  with ide arduino, I remember it was in English I don't know if it exist in espnol

carlosimparato, 2021-06-15:
el idioma no importa, el problema cuando conecto la linkit a mi computador no hace nada, no suena, no me dice nada, como si el linkit no estuviese conectado. he instalado varios controladores pero ninguno reconoce al linkit. he llegado a pensar que la placa esta dañada.

wudikukuqi, 2021-06-16:
> Thank you for the update... I can’t find any here who got that! Have any of you used any other Arduino chip for this project?

Which country are you in? I have two pieces of surplus here, which can be transferrable to you.

carlosimparato, 2022-01-11:
Hola de nuevo. los programas de python que trae la carpeta de software, hay que cargarlos en la linkit? yo cargue el archivo de arduino perfectamente pero no se que hacer con los archivos de python.   Una ayudita por favor.  mil gracias.

vertigo475, 2022-01-11:
Buenos dias,
gracias por tu mensaje.

No necesitaba los archivos de python. solo arduino

Buenas tardes
olivier

LuardG247, 2024-07-11:
Hello vertigo475,i'm new to this kind of project so hope i could be ask for your help.Can you show me what is the degree of each servo when you assemble it into the leg? Many thank for you support.

vertigo475, 2024-07-11:
________________________________
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

vertigo475, 2024-07-11:
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

vertigo475, 2024-07-11:
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

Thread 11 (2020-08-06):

Lipo Nattern

dirk-asam, 2020-08-06:
Could anyone Tell me what size ( - Else Size in mAh) the lipo battery has?

Thanks

vertigo475, 2020-08-14:
Hi, I've put an 2S lipo 2200mah it fits well ;)

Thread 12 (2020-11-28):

3D-Printed Parts do not fit together

TimKlaas, 2020-11-28:
Hey,

we tried to rebuild the Hexapod as described, but after printing all the parts we noticed that they not fit together properly and when taking a look at the STL files the sizes also dont match up. One example would be connecting the foot_top and foot_tip or the fitting for the motor. What is the reason for that, did we miss something?

MRCamiloLagos, 2020-12-04:
can you help me? i need to get the screw/bolts that are used where i can get in internet? i think the size are 1M ?
I From Honduras i would appreciate i need for a project camiloflores1986@hotmail.com my email

@MRCamiloLagos

rx290, 2024-11-14:
There is this calculator which help you resize the fitting items, here is the link for it, clone it and let me know if this worked for you.
https://docs.google.com/spreadsheets/d/1LO37kJxJx8rW_mv_S8CdKpyp7A_Vs2d3BoclptP_St4/edit?gid=0#gid=0

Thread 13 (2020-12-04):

screw/bolts sizes

MRCamiloLagos, 2020-12-04:
can you somebody help me?  i need to get the screw/bolts that are used where i can get in internet? i think the size are 1M ?
 I From Honduras i would appreciate i need for a project camiloflores1986@hotmail.com my email

schnello, 2021-01-20:
Take a loot to the BOM: https://github.com/SmallpTsai/hexapod-v2-7697/blob/master/mechanism/BOM.md
All screws are listed

MRCamiloLagos, 2021-01-20:
I thought the hexapod Leg Assembly leg bolts were M1..

I look M2  a little big but thanks... i will try with M2

MRCamiloLagos, 2021-01-20:
Thanks My Friend  and this video https://www.youtube.com/watch?v=oaAE5fC09KQ&feature=emb_logo they used M1?
[https://i.ytimg.com/vi/oaAE5fC09KQ/maxresdefault.jpg]<https://www.youtube.com/watch?v=oaAE5fC09KQ&feature=emb_logo>
Hexapod Leg Assembly - YouTube<https://www.youtube.com/watch?v=oaAE5fC09KQ&feature=emb_logo>
Hexapod v2.1 - Leg assembly instructionThis video demostrate how to seemble 1 Leg of Hexapod (total 6 required)For hexpod running video, please check https:/...
www.youtube.com

Camilo?? FLores
97738475
Manten la cabeza en la direccion Correcta, y no tendras que preocuparte por tus Pies..

________________________________
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

schnello, 2021-01-30:
I build it with M2 and M2 fits perfect:
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

MRCamiloLagos, 2021-02-08:
THANKS MAN last question do you have a link where to get it in Internet amazon o something i want buy from Amazon

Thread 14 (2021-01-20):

PCB Order

schnello, 2021-01-20:
Hello.

I order for this project 5 pcs main and 10 pcs sub boards. (should arrive in 4 weeks)
I need onle 1 set so if anyone needs a PCB you can get it for the real purchase price and shipping costs (location is Europe Austria) please contact me (schnello.android@gmail.com),
Price is 2.5€ exl shipping (only Europe)

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

schnello, 2021-02-15:
all sold

Closed 2021-02-15.

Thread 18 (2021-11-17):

Please change LinkIt 7697. We cant find this :( . Many people like your project!!! But we cant find LinkIt 7697 : ( . And Thanx your work!!!

LhamoJam, 2021-11-17:
Please change LinkIt 7697. We cant find this :( . Many people like your project!!! But we cant find LinkIt 7697 : ( . And Thanx your work!!!

LhamoJam, 2021-11-17:
Some country buy linkit7697 have to wait 3 moth to get Linkit 7697 : (

Tomtom5893, 2021-11-25:
I got one but i cant find the sdk so i cant flash them with the arduino software...

Tomtom5893, 2021-11-25:
https://www.amazon.de/AZDelivery-ESP32-NodeMCU-gratis-eBook/dp/B07Z83MF5W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

Maybe this one will do it?

it has the same hardware specs (at least thats what i can say)
maybe it needs a little bit of code change but then you are good to go

rookiepeng, 2022-01-01:
I have made it work with Raspberry Pi Zero W. Increased the body width a little, and full rework on the electronic and software.
https://github.com/rookiepeng/hexapod

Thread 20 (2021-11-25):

Linkit SDK is not online anymore...

Tomtom5893, 2021-11-25:
I need the Linkit SDK to upload a program to my linkit 7697.

It looks like mediathek has removed the sd from there page.

Does anyone have a working link for me?

Maybe we can include them in the software folder...

mikeq3, 2021-12-16:
In the Arduino IDE preferences tab put this URL in the "Additional Boards Manager URLs" field:
http://download.labs.mediatek.com/package_mtk_linkit_7697_index.json

That should get you going.

Tomtom5893, 2021-12-17:
Thank you so much that works

Closed 2021-12-17.

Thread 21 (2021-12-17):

I have spare PCB's if someone want.

Tomtom5893, 2021-12-17:
I ordered more PCB's as needed because I didn't know if something was going wrong.
I still have some available if someone wants them.

(Shipped from Germany)

Bachir-Tarif, 2021-12-17:
Hi, im a student i am currently bulding the hexapode if you could do the
shipping i am in France.

Le ven. 17 déc. 2021 à 13:07, Tomtom5893 ***@***.***> a
écrit :

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

Tomtom5893, 2021-12-17:
@Bachir-Tarif can you send me your mail without @ like example(at)something(dot)com ?

Bachir-Tarif, 2021-12-17:
I didn't understand exactly, you mean like this:
***@***.***

Le ven. 17 déc. 2021 à 15:32, Tomtom5893 ***@***.***> a
écrit :

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

Tomtom5893, 2021-12-17:
github censors the emails. if you send me the email the normal way it looks like this example@yahoo.com but if you send it like this example (at) yahoo (dot) com it works

Bachir-Tarif, 2021-12-17:
Aah ok, then it's
bachir.cpu(At)gmail( dot)com

Le ven. 17 déc. 2021 à 15:52, Tomtom5893 ***@***.***> a
écrit :

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

Tomtom5893, 2021-12-17:
> Aah ok, then it's bachir.cpu(At)gmail( dot)com Le ven. 17 déc. 2021 à 15:52, Tomtom5893 ***@***.***> a écrit :
> […](#)
> github censors the emails. if you send me the email the normal way it looks like this ***@***.*** but if you send it like this example (at) yahoo (dot) com it works — Reply to this email directly, view it on GitHub <[#21 (comment)](https://github.com/SmallpTsai/hexapod-v2-7697/issues/21#issuecomment-996781336)>, or unsubscribe <https://github.com/notifications/unsubscribe-auth/AV2UQA3FVETHHKVFA4MZWR3URNFCLANCNFSM5KIWAZNQ> . Triage notifications on the go with GitHub Mobile for iOS <https://apps.apple.com/app/apple-store/id1477376905?ct=notification-email&mt=8&pt=524675> or Android <https://play.google.com/store/apps/details?id=com.github.android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>. You are receiving this because you were mentioned.Message ID: ***@***.***>

I send you Email. did you receive it? if so, you can delete your comment

Lorenzik66, 2021-12-25:
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

bonjour, je suis intéressé pour fabriquer le mien , comment peut on faire ? je suis en france.
voici mon mail : courrierlorenzo😀gmail(dat)com
merci d’avance et joyeux noël

GGabi0101, 2023-02-21:
Moin könntest du mir auch deine Email wie oben beschrieben schreiben? wäre an einem pcb set interessiert

Tomtom5893, 2023-02-21:
> interessiert

tomtom5893 [at] Gmail.com

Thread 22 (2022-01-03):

Alternate servo motors

pulkitvyas08, 2022-01-03:
If I cannot find the specified servo model `MG92B` then can I use other motors like `SG90S` or `MG995`? The major concern here is if the 3D print designs are compatible with those motors

ValeraDanger, 2022-01-04:
https://github.com/SmallpTsai/hexapod-v2-7697/issues/6#issuecomment-1005206797

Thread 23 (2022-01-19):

STL files and source Code

nasrabdalhakeem, 2022-01-19:
The STL files I can't download it, and can you guid me where is the UI application and source of it and the major code to move the hexapod robot.

rx290, 2024-11-14:
open a terminal/cmd/powershell in a folder where you want to download it type git clone 'paste link of the repo here' and it will clone everything for you on your device.

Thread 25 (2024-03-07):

Can I replace mg92b steering gear with another steering gear?

tianyi725, 2024-03-07:
Can I replace mg92b steering gear with another steering gear? It's too expensive

(But I was worried that the hexapod would become worse because I had changed to a cheaper steering gear.）

thank you！

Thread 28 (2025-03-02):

Information from my research to run and compile the project correctly (02.03.2025)

screamerMZ, 2025-03-02:
Information from my research to run and compile the project correctly:

1. Install Arduino IDE 1.8.15
2. Additional URL to the board manager for LinkIt 7697

    File →  Preferences →  Additional URLs to the board manager
    paste URL: https://files.gitbook.com/v0/b/gitbook-x-prod.appspot.com/o/spaces%2FY4gduUSLWOCI23CXUWej%2Fuploads%2FGxrukfmWpd9mgElwxZaW%2Fpackage_mtk_linkit_7697_index.json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

3. Now install LinkIt 7697 support:

    Tools → Board → Board Manager
    Search for LinkIt 7697
    Install version 0.10.21.

4. Add libraries in the specified versions:

      Sketch → Include Library → Manage Libraries

      Search and install:
                                      Adafruit PWM Servo Driver (**version 2.4.0**)
                                      Adafruit BusIO (**version 1.7.3**)

5. Remove folder:
          C:\Users\<user>\AppData\Local\Arduino15\packages\LinkIt\hardware\linkit_rtos\0.10.21\libraries\Light_Sensor_LM358

to prevent compilation errors due to missing files

6. For Hexapod control via BLE (Android Phone) download and install apk from: [](https://apkpure.com/linkit-remote/com.mediatek.labs.linkitremote)

That's all ! :)

Open .ino project, compile, upload and have fun! :)

Cheers!

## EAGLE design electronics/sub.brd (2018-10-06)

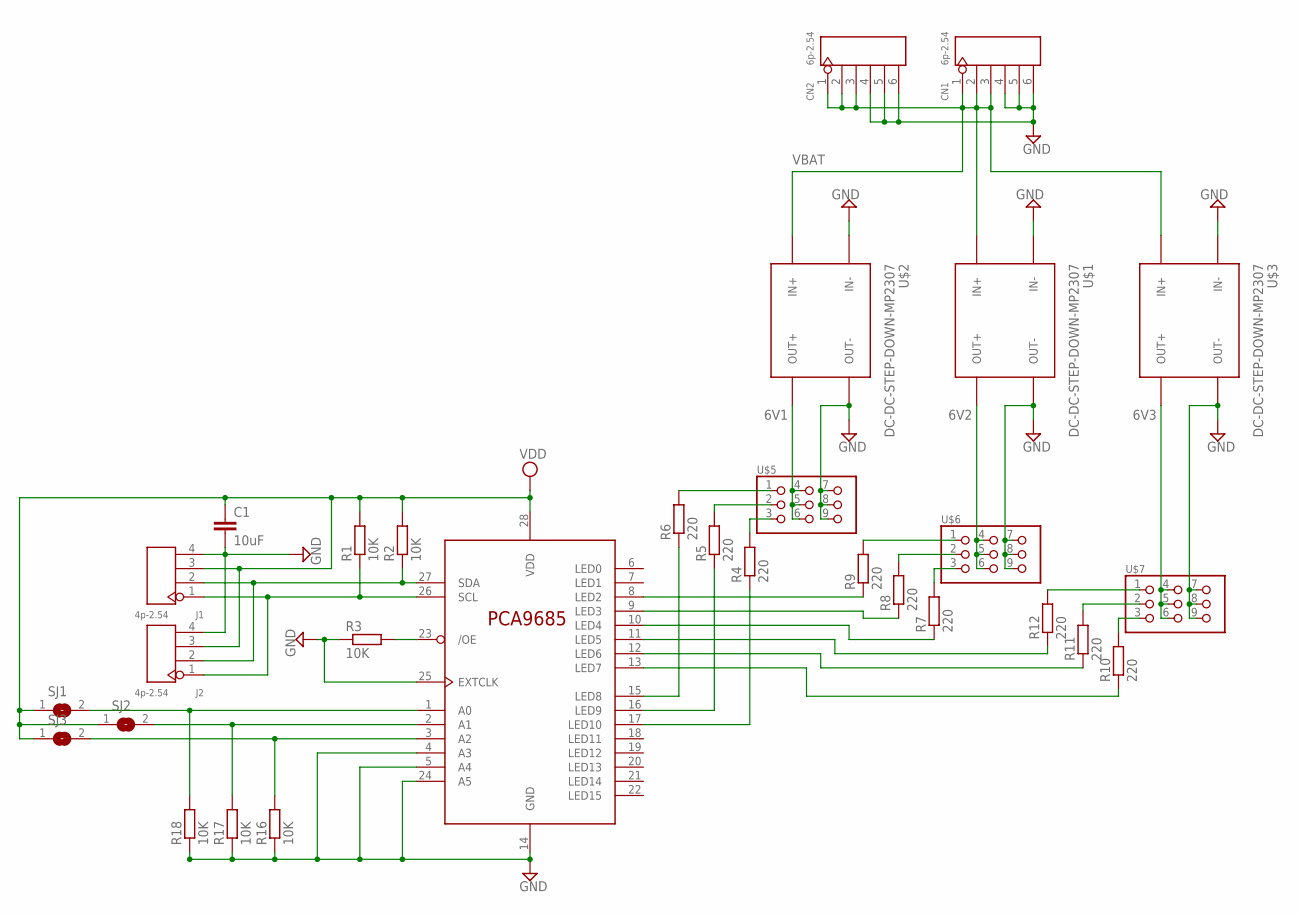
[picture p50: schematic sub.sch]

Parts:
C1: 10uF; C0805
CN1, CN2: 6p-2.54; H6-2.54
J1, J2: 4p-2.54; H4-2.54
R1, R2, R3, R16, R17, R18: 10K; M0805
R4, R5, R6, R7, R8, R9, R10, R11, R12: 220; M0805
SJ1, SJ2, SJ3: SJ
U$1, U$2, U$3: DC-DC-STEP-DOWN-MP2307
U$4: PCA9685PW; TSSOP28
U$5, U$6, U$7: PIN_3X3

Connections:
6V1: U$2.OUT+, U$5.4, U$5.5, U$5.6
6V2: U$1.OUT+, U$6.4, U$6.5, U$6.6
6V3: U$3.OUT+, U$7.4, U$7.5, U$7.6
GND: C1.2, CN1.4, CN1.5, CN1.6, CN2.4, CN2.5, CN2.6, J1.4, J2.4, R3.1, R16.1, R17.1, R18.1, U$1.IN-, U$1.OUT-, U$2.IN-, U$2.OUT-, U$3.IN-, U$3.OUT-, U$4.4 (A3), U$4.5 (A4), U$4.14 (GND), U$4.24 (A5), U$4.25 (EXTCLK), U$5.7, U$5.8, U$5.9, U$6.7, U$6.8, U$6.9, U$7.7, U$7.8, U$7.9
unnamed: J1.1, J2.1, R1.1, U$4.26 (SCL)
unnamed: R6.1, U$4.15 (LED8)
unnamed: R3.2, U$4.23 (/OE)
unnamed: R5.1, U$4.16 (LED9)
unnamed: R4.1, U$4.17 (LED10)
unnamed: R9.1, U$4.8 (LED2)
unnamed: R8.1, U$4.9 (LED3)
unnamed: R7.1, U$4.10 (LED4)
unnamed: R11.1, U$4.12 (LED6)
unnamed: R4.2, U$5.3
unnamed: R5.2, U$5.2
unnamed: R6.2, U$5.1
unnamed: R9.2, U$6.1
unnamed: R8.2, U$6.2
unnamed: R7.2, U$6.3
unnamed: R10.1, U$4.13 (LED7)
unnamed: R12.1, U$4.11 (LED5)
unnamed: R12.2, U$7.1
unnamed: R11.2, U$7.2
unnamed: R10.2, U$7.3
unnamed: R16.2, SJ3.2, U$4.3 (A2)
unnamed: R17.2, SJ2.2, U$4.2 (A1)
unnamed: R18.2, SJ1.2, U$4.1 (A0)
unnamed: J1.2, J2.2, R2.1, U$4.27 (SDA)
VBAT: CN1.1, CN1.2, CN1.3, CN2.1, CN2.2, CN2.3, U$1.IN+, U$2.IN+, U$3.IN+
VDD: C1.1, J1.3, J2.3, R1.2, R2.2, SJ1.1, SJ2.1, SJ3.1, U$4.28 (VDD)

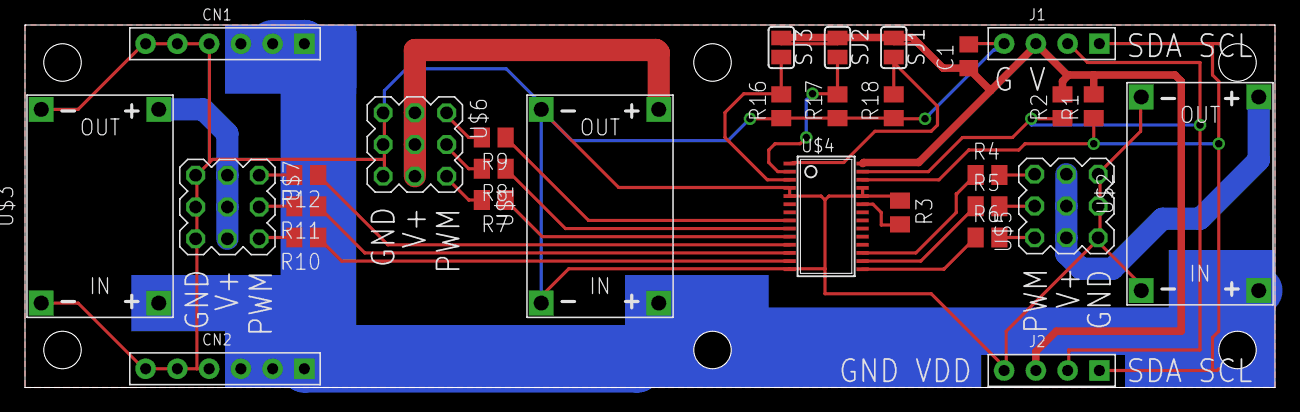
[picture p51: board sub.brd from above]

Board: 2 copper layers, 100.0 x 29.0 mm, 30 parts (0 on the bottom side), 30 nets.

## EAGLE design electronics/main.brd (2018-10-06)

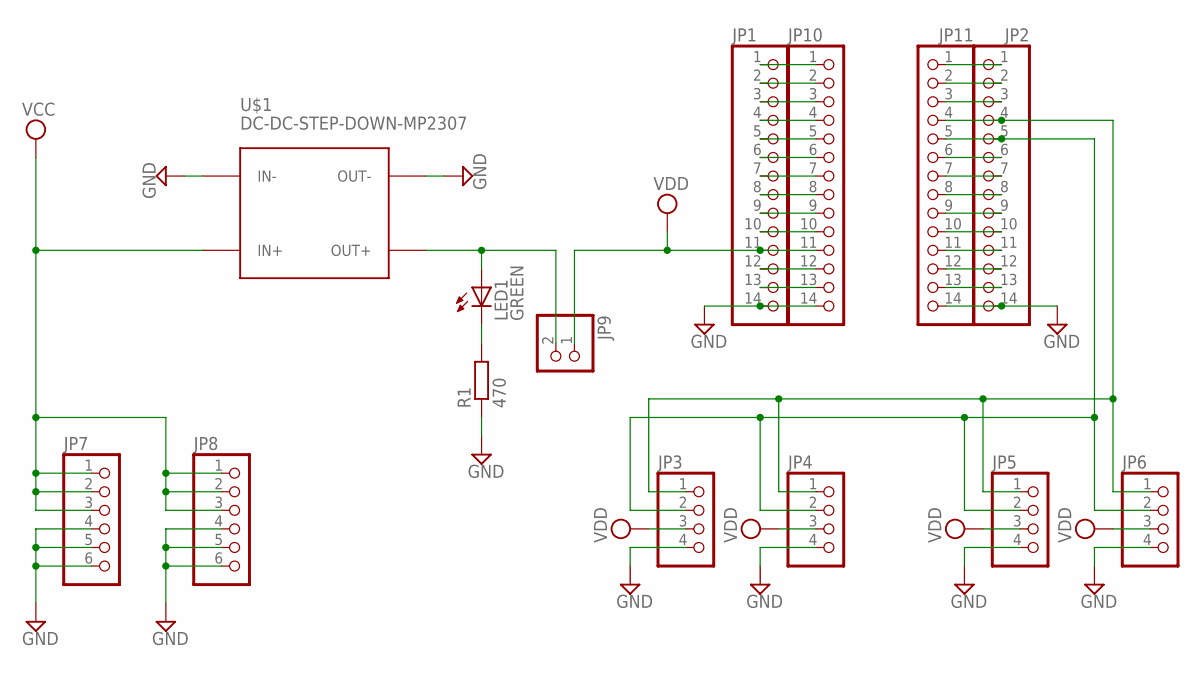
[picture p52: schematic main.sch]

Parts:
JP1, JP2, JP10, JP11: PINHD-1X14_2.54; 1X14
JP3, JP4: PINHD-1X4_2.54-90°; 1X04/90
JP5, JP6: PINHD-1X4_2.54; 1X04
JP7, JP8: PINHD-1X6_2.54-90°; 1X06/90
JP9: PINHD-1X2_2.54; 1X02
LED1: GREEN; CHIP-LED0805
R1: 470; R0805
U$1: DC-DC-STEP-DOWN-MP2307

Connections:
+5V: JP9.2, LED1.A, U$1.OUT+
GND: JP1.14, JP2.14, JP3.4, JP4.4, JP5.4, JP6.4, JP7.4, JP7.5, JP7.6, JP8.4, JP8.5, JP8.6, JP10.14, JP11.14, R1.1, U$1.IN-, U$1.OUT-
unnamed: JP1.1, JP10.1
unnamed: JP1.2, JP10.2
unnamed: JP1.3, JP10.3
unnamed: LED1.C, R1.2
unnamed: JP1.4, JP10.4
unnamed: JP1.5, JP10.5
unnamed: JP1.6, JP10.6
unnamed: JP1.7, JP10.7
unnamed: JP1.8, JP10.8
unnamed: JP1.9, JP10.9
unnamed: JP1.10, JP10.10
unnamed: JP1.12, JP10.12
unnamed: JP1.13, JP10.13
unnamed: JP2.1, JP11.1
unnamed: JP2.2, JP11.2
unnamed: JP2.3, JP11.3
unnamed: JP2.6, JP11.6
unnamed: JP2.7, JP11.7
unnamed: JP2.8, JP11.8
unnamed: JP2.9, JP11.9
unnamed: JP2.10, JP11.10
unnamed: JP2.11, JP11.11
unnamed: JP2.12, JP11.12
unnamed: JP2.13, JP11.13
SCL: JP2.4, JP3.1, JP4.1, JP5.1, JP6.1, JP11.4
SDA: JP2.5, JP3.2, JP4.2, JP5.2, JP6.2, JP11.5
VCC: JP7.1, JP7.2, JP7.3, JP8.1, JP8.2, JP8.3, U$1.IN+
VDD: JP1.11, JP3.3, JP4.3, JP5.3, JP6.3, JP9.1, JP10.11

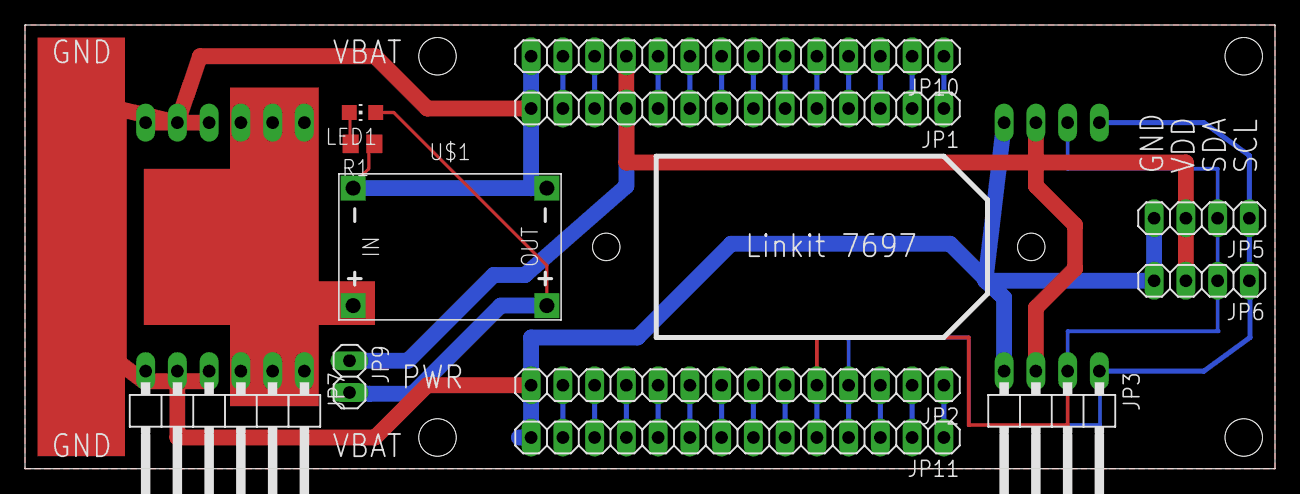
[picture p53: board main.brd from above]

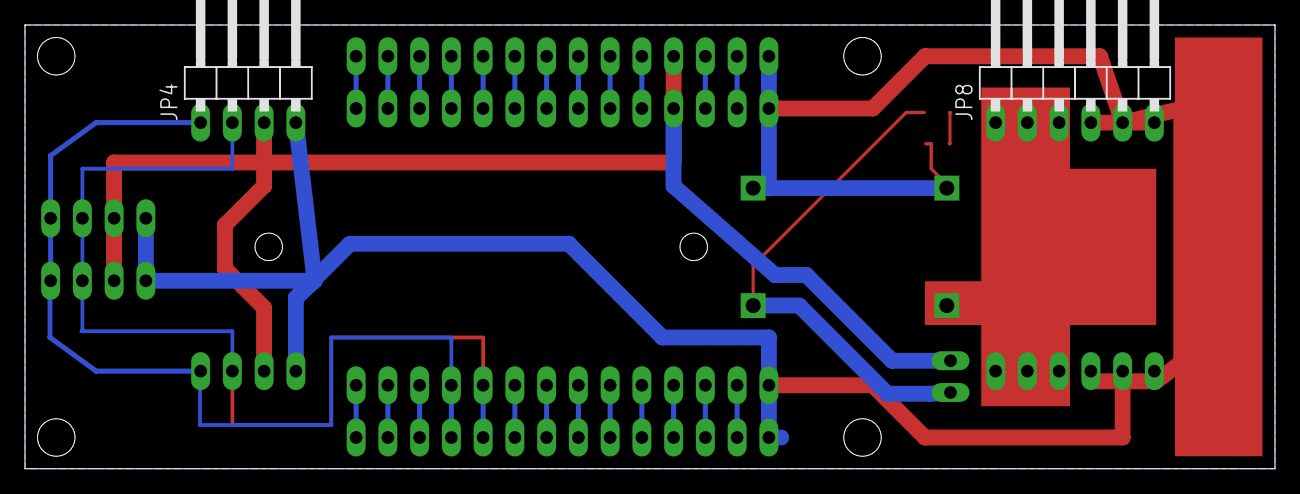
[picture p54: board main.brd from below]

Board: 2 copper layers, 100.0 x 35.5 mm, 14 parts (2 on the bottom side), 30 nets.

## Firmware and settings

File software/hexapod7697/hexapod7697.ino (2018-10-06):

#include "src/setting_mode.h"
#include "src/normal_mode.h"

#include "src/hexapod/debug.h"
#include "src/hexapod/hexapod.h"

//
//  mode
//    0:  normal mode
//    1:  setting mode (for servo calibration)
//
static int _mode = 0;

static void log_output(const char* log) {
  Serial.println(log);
}

//
// wait for N secs, enter setting mode if pressed USR button
//
void boot_wait(int wait_for = 2000) {
  digitalWrite(LED_BUILTIN, HIGH);

  pinMode(6, INPUT);
  while (wait_for > 0) {
    if (HIGH == digitalRead(6)) {
      _mode = 1;
      break;
    }
    delay(100);
    wait_for -= 100;
  }

  digitalWrite(LED_BUILTIN, LOW);
}

//
//  Do common setup and mode-specific setup
//
void setup() {
  //Initialize serial and wait for port to open:
  Serial.begin(115200);
  Serial.println("Starting...");

  //
  // Common setup()
  //

  // Initialize GPIO
  pinMode(LED_BUILTIN, OUTPUT);

  // Workaround for beta PCB
  pinMode(2, INPUT);
  pinMode(3, INPUT);

  boot_wait();

  hexapod::initLogOutput(log_output, millis);
  hexapod::Hexapod.init(_mode == 1);

  //
  // Mode-specific setup()
  //

  if (_mode == 0) {
    normal_setup();
  }
  else if (_mode == 1) {
    setting_setup();
  }

  Serial.print("Started, mode=");
  Serial.println(_mode);
}

void loop() {
  if (_mode == 0) {
    normal_loop();
  }
  else if (_mode == 1) {
    setting_loop();
  }
}

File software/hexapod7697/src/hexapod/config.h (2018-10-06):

#pragma once

namespace hexapod { 

    namespace config {
        // all below definition use unit: mm
        const float kLegMountLeftRightX = 29.87;
        const float kLegMountOtherX = 22.41;
        const float kLegMountOtherY = 55.41;
        
        const float kLegRootToJoint1 = 20.75;
        const float kLegJoint1ToJoint2 = 28.0;
        const float kLegJoint2ToJoint3 = 42.6;
        const float kLegJoint3ToTip = 89.07;


        // timing setting. unit: ms
        const int movementInterval = 5;
        const int movementSwitchDuration = 150;
    }

}

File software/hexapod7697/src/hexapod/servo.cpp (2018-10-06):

#include "servo.h"
#include "debug.h"

#include "hal/pwm.h"

namespace hexapod { 

    namespace {
        // if freq = 240, 1 tick = 1000000 / (240*4096) ~= 1us
        // if freq = 120, 1 tick = 1000000 / (120*4096) ~= 2us
        const static int kFrequency = 120;
        const static int kTickUs = 2;
        const static int kServoMiddle = 1400;
        const static int kServoMax = 2000;
        const static int kServoMin = 800;
        const static int kServoRange = kServoMax-kServoMiddle;

        auto pwmLeft = hal::PCA9685(0x41);
        auto pwmRight = hal::PCA9685(0x40);
        bool pwmInited = false;
 
        void initPWM(void) {
            if (pwmInited)
                return;

            pwmLeft.begin();  
            pwmLeft.setPWMFreq(kFrequency);
            pwmRight.begin();  
            pwmRight.setPWMFreq(kFrequency);
            pwmInited = true;
        }

        int hexapod2pwm(int legIndex, int partIndex) {
            switch(legIndex) {
            case 0:     return 5 + partIndex;
            case 1:     return 2 + partIndex;
            case 2:     return 8 + partIndex;
            case 3:     return 16 + 8 + partIndex;
            case 4:     return 16 + 2 + partIndex;
            case 5:     return 16 + 5 + partIndex;
            default:    return 0;
            }
        }

        int pwm2hexapod(int pwm) {
            if(pwm >= 16+8)
                return 9 + pwm - (16+8);
            if(pwm >= 16+5)
                return 15 + pwm - (16+5);
            if(pwm >= 16+2)
                return 12 + pwm - (16+2);
            if(pwm >= 8)
                return 6 + pwm - (8);
            if(pwm >= 5)
                return 0 + pwm - (5);
            if(pwm >= 2)
                return 3 + pwm - (2);
            return -1;
        }

    }

    void Servo::init(void) {
        initPWM();
    }

    Servo::Servo(int legIndex, int partIndex) {
        pwmIndex_ = hexapod2pwm(legIndex, partIndex);
        inverse_ = partIndex == 1 ? true : false;
        adjust_angle_ = partIndex == 1 ? 15.0 : 0.0;
        range_ = partIndex == 0 ? 45 : 60;
        angle_ = 0;
    }

    void Servo::setAngle(float angle) {
        initPWM();

        if (angle > range_ + adjust_angle_) {
            LOG_INFO("exceed[%d][%f]", pwm2hexapod(pwmIndex_), angle);
            angle = range_;
        }
        else if(angle < -range_ + adjust_angle_) {
            LOG_INFO("exceed[%d][%f]", pwm2hexapod(pwmIndex_), angle);
            angle = -range_;
        }

        angle_ = angle;

        hal::PCA9685* pwm;
        int idx;
        if (pwmIndex_ < 16) {
            pwm = &pwmRight;
            idx = pwmIndex_;
        }
        else {
            pwm = &pwmLeft;
            idx = pwmIndex_ - 16;
        }
        angle -= adjust_angle_;
        if (inverse_)
            angle = -angle;

        int us = kServoMiddle + offset_ + angle*(kServoRange/60)*(1+0.01*scale_);
        if (us > kServoMax)
            us = kServoMax;
        else if(us < kServoMin)
            us = kServoMin;

        pwm->setPWM(idx, 0, us/kTickUs);
        LOG_DEBUG("setAngle(%.2f, %d)", angle, us);
    }

    float Servo::getAngle(void) {
        return angle_;
    }

}

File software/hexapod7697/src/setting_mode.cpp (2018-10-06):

#include <Arduino.h>

#ifndef __LREMOTE_H__
#include <LRemote.h>
#define __LREMOTE_H__
#endif

#include "linkit_control/ui_controls.h"
#include "hexapod/debug.h"
#include "hexapod/hexapod.h"

#define WIDTH 9
#define HEIGHT 18
#define L_W WIDTH
#define L_H 1
#define B_W 2
#define B_H 2
#define T_W 5
#define T_H 2

#define L_X(g)  0
#define L_Y(g)  (L_H+T_H)*g
#define Bl_X(g)  0
#define Bl_Y(g)  (L_H+T_H)*g+L_H
#define T_X(g)  B_W
#define T_Y(g)  (L_H+T_H)*g+L_H
#define Br_X(g)  B_W+T_W
#define Br_Y(g)  (L_H+T_H)*g+L_H

//---------------------------------------------------------------------------
// UI Group: Adjust setting

static Label label1("Select leg", L_X(0), L_Y(0), L_W, L_H);
static Label text1("", T_X(0), T_Y(0), T_W, T_H, RC_PINK);
static Button button1l(10, "<", Bl_X(0), Bl_Y(0), B_W, B_H, RC_BLUE);
static Button button1r(11, ">", Br_X(0), Br_Y(0), B_W, B_H, RC_BLUE);

static Label label2("Select joint", L_X(1), L_Y(1), L_W, L_H);
static Label text2("", T_X(1), T_Y(1), T_W, T_H, RC_PINK);
static Button button2l(20, "<", Bl_X(1), Bl_Y(1), B_W, B_H, RC_BLUE);
static Button button2r(21, ">", Br_X(1), Br_Y(1), B_W, B_H, RC_BLUE);

static Label label3("Servo offset", L_X(2), L_Y(2), L_W, L_H);
static Label text3("0", T_X(2), T_Y(2), T_W, T_H, RC_PINK);
static Button button3l(30, "-", Bl_X(2), Bl_Y(2), B_W, B_H, RC_BLUE);
static Button button3r(31, "+", Br_X(2), Br_Y(2), B_W, B_H, RC_BLUE);

static Label label4("Servo scale", L_X(3), L_Y(3), L_W, L_H);
static Label text4("0", T_X(3), T_Y(3), T_W, T_H, RC_PINK);
static Button button4l(40, "-", Bl_X(3), Bl_Y(3), B_W, B_H, RC_BLUE);
static Button button4r(41, "+", Br_X(3), Br_Y(3), B_W, B_H, RC_BLUE);

static Button buttonSave(60, "Save", 0, Bl_Y(5), WIDTH, B_H, RC_GREEN);

static ButtonGroup btnGroup;

//---------------------------------------------------------------------------
// UI Group: Test

static Label label5("Servo test", L_X(4), L_Y(4), L_W, L_H);
static Button button5l(-45, "-45°", 0, Bl_Y(4), WIDTH/3, B_H, RC_YELLOW);
static Button button5c(0, "0°", WIDTH/3, Bl_Y(4), WIDTH/3, B_H, RC_YELLOW);
static Button button5r(45, "+45°", WIDTH*2/3, Bl_Y(4), WIDTH/3, B_H, RC_YELLOW);

static ButtonGroup btnGroupTest;

//---------------------------------------------------------------------------

const static String _leg_table[] = {
  "front right",
  "right",
  "rear right",
  "rear left",
  "left",
  "front left",
};

const static String _joint_table[] = {
  "body",
  "thigh",
  "foot",
};

static int _cur_leg = 0;
static int _cur_joint = 0;
static int _cur_offset = 0;
static int _cur_scale = 0;
static int _test_angle[3*6] = {0};

void update_text(void) {
  text1.updateText(_leg_table[_cur_leg]);
  text2.updateText(_joint_table[_cur_joint]);
  text3.updateText(String(_cur_offset));
  text4.updateText(String(1+0.01*_cur_scale));
}

static uint8_t led_blink_state = 0;

void setting_setup(void) {

  digitalWrite(LED_BUILTIN, HIGH);

  //
  // initialize config mode UI
  //
  LRemote.setName("Hexapod (S)");
  LRemote.setOrientation(RC_PORTRAIT);
  LRemote.setGrid(WIDTH, HEIGHT);

  LRemote_addControls({
    &label1, &text1, &button1l, &button1r,  // row1
    &label2, &text2, &button2l, &button2r,  // row2
    &label3, &text3, &button3l, &button3r,  // row3
    &label4, &text4, &button4l, &button4r,  // row4
    &label5, &button5l, &button5c, &button5r, // row5
    &buttonSave                             // row6
  });

  //
  // Button group
  //  
  btnGroup.addControls({
    &button1l, &button1r,
    &button2l, &button2r,
    &button3l, &button3r,
    &button4l, &button4r,
    &buttonSave
  });

  btnGroup.config([](int btn_id, ButtonGroup::mode mode) {
    if (mode != ButtonGroup::mode::DOWN && mode != ButtonGroup::mode::REPEAT)
      return;

    Serial.print("button id: ");
    Serial.print(String(btn_id));
    Serial.println(" is triggered");

    int g = btn_id / 10;
    int lr = btn_id % 10;

    switch(g) {
    case 1:
      _cur_leg = (_cur_leg + 6 + (lr ? 1 : -1)) % 6;
      hexapod::Hexapod.calibrationGet(_cur_leg, _cur_joint, _cur_offset, _cur_scale);
      hexapod::Hexapod.calibrationTest(_cur_leg, _cur_joint, _test_angle[_cur_leg*3+_cur_joint]);
      break;
    case 2:
      _cur_joint = (_cur_joint + 3 + (lr ? 1 : -1)) % 3;
      hexapod::Hexapod.calibrationGet(_cur_leg, _cur_joint, _cur_offset, _cur_scale);
      hexapod::Hexapod.calibrationTest(_cur_leg, _cur_joint, _test_angle[_cur_leg*3+_cur_joint]);
      break;
    case 3:
      _cur_offset += (lr ? 1 : -1);
      hexapod::Hexapod.calibrationSet(_cur_leg, _cur_joint, _cur_offset, _cur_scale);
      break;
    case 4:
      _cur_scale += (lr ? 1 : -1);
      hexapod::Hexapod.calibrationSet(_cur_leg, _cur_joint, _cur_offset, _cur_scale);
      break;
    case 6:
      hexapod::Hexapod.calibrationSave();
    }
    update_text();
  });

  //
  // Button group: Testing
  //  
  btnGroupTest.addControls({
    &button5l, &button5c, &button5r
  });
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

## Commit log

2018-09-21 add screw part
2018-09-23 add more BOM images
2018-10-06 add sch and src
    [main.brd, main.sch, sub.brd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]
2018-10-07 add stl part
    [battery_lock.stl, body_back_wall.stl, body_bottom.stl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]
2018-10-08 add leg assemble instruction
2018-12-09 update to lock-based joint
    [body_bottom.stl, body_side_wall.stl, body_top.stl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]
2019-05-15 Added fixed joint_cross.stl by jmfinn9
    [joint_cross.stl]
2019-05-15 Fixed leg_bottom.stl
    [leg_bottom.stl]

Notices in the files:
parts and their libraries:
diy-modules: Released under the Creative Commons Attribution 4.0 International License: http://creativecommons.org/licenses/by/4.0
